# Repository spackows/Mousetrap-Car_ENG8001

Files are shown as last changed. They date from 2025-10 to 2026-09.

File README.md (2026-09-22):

# Mousetrap Car
Group project for: **ENG8001 - Principles of Design**, [Bachelor of Engineering (Automation and Robotics Engineering) (Co-op)](https://www.algonquincollege.com/sat/program/bachelor-of-automation-and-robotics/)

<p>&nbsp;</p>

## Background

### Mousetrap cars in STEM education
Sooner or later, most science, engineering, or design students build a [mousetrap car](https://en.wikipedia.org/wiki/Mousetrap_car). :)

Details vary, but most projects focus on building a small car that is powered by a spring-loaded bar type of mousetrap. Mousetrap car builders sometimes compete to see who can build a car that achieves maximum speed or maximum distance.

### Our project goals
1. Build a mousetrap car that travels 20 feet as efficiently as possible while autonomously navigating around an 8-inch x 4-inch obstacle at a variable distance in the center of a 4-foot-wide track.
2. Learn to apply engineering design principles and practices.

<p>&nbsp;</p>

## Design conception

### Objectives
We identified 5 objectives:
1. Go fast – Be in the top 25% fastest results
2. Sense object – Detect object 100% of the time
3. Avoid object – Avoid the object 100% of the time
4. Stay on the track/cross the finish – Even if we are not the fastest, complete the course every run
5. Consistent performance – Successfully detect and avoid the object every run; and the time of our runs will not vary by more than 10%

To prioritize these objectives, we used a pairwise comparison matrix.  For each cell, a 1 is assigned if the objective in that row is more important than the objective in that column.  Then, for each row, the sum of the 1's is the score for the objective in that row.

Table 1: Pairwise comparison of objectives
<table>
<tr>
<td>&nbsp;</td>
<td align="center">Go fast</td>
<td align="center">Sense object</td>
<td align="center">Avoid object</td>
<td align="center">Stay on track</td>
<td align="center">Consistent</td>
<td align="center"><b>Score</b></td>
</tr>
<tr>
<td>Go fast</td>
<td align="center">x</td>
<td align="center">0</td>
<td align="center">0</td>
<td align="center">0</td>
<td align="center">1</td>
<td align="center"><b>1</b></td>
</tr>
<tr>
<td>Sense object</td>
<td align="center">1</td>
<td align="center">x</td>
<td align="center">0</td>
<td align="center">0</td>
<td align="center">1</td>
<td align="center"><b>2</b></td>
</tr>
<tr>
<td>Avoid object</td>
<td align="center">1</td>
<td align="center">1</td>
<td align="center">x</td>
<td align="center">1</td>
<td align="center">1</td>
<td align="center"><b>4</b></td>
</tr>
<tr>
<td>Stay on track</td>
<td align="center">1</td>
<td align="center">1</td>
<td align="center">0</td>
<td align="center">x</td>
<td align="center">1</td>
<td align="center"><b>3</b></td>
</tr>
<tr>
<td>Consistent</td>
<td align="center">0</td>
<td align="center">0</td>
<td align="center">0</td>
<td align="center">0</td>
<td align="center">x</td>
<td align="center"><b>0</b></td>
</tr>
</table>

### Key functions
We identified key functions:
1. How is power transferred from the spring to the wheels?
2. How is the object sensed?
3. How is the object avoided?
4. How is steering accomplished?
5. How will the car stay on the track?
6. How will speed be optimized?

We used a morphological table to define the space of our early conceptual solutions.

Table 2: Morphological table
<table>
<tr>
<td align="center"><b>Function</b></td>
<td  align="center" colspan="3"><b>Means</b></td>
</tr>
<tr>
<td valign="top">Transfer power from spring</td>
<td valign="top">Tie a string from the hammer to around the axle</td>
<td valign="top">Attach an extension to the hammer and tie the string to that for greater leverage</td>
<td valign="top">Attach a "foot" to the hammer so that when the spring unwinds, the foot pushes against the ground</td>
</tr>
<tr>
<td valign="top">Sense object</td>
<td valign="top">Ultrasonic sensor</td>
<td valign="top">Camera</td>
<td valign="top">"Feeler" (like antennae or whiskers)</td>
</tr>
<tr>
<td valign="top">Avoid object</td>
<td valign="top">Steer around the object</td>
<td valign="top">Jump over the object</td>
<td valign="top">Use the object itself to push the car around (like a spinning bumper)</td>
</tr>
<tr>
<td valign="top">Stay on Track</td>
<td valign="top">Detect the tape at the edges using a camera and steer away from them</td>
<td valign="top">Steer a trajectory that passes close to the object (because it’s in the middle)</td>
<td valign="top">Programmatically limit steering to maintain an overall straight displacement</td>
</tr>
<tr>
<td valign="top">Steering</td>
<td valign="top">Use a motor to pivot the front axle</td>
<td valign="top">Use a weight to lean to turn the wheels (like a skateboard)</td>
<td valign="top">Temporarily drop an anchor to pull the car to the left or right</td>
</tr>
<tr>
<td valign="top">Speed</td>
<td valign="top">Use 3 wheels instead of 4 to reduce friction from wheels</td>
<td valign="top">Make the car aerodynamic</td>
<td valign="top">Start the car on an angle to reduce the number of turns needed</td>
</tr>
</table>

### Sketches
Whiteboard sketches from brainstorming concepts:

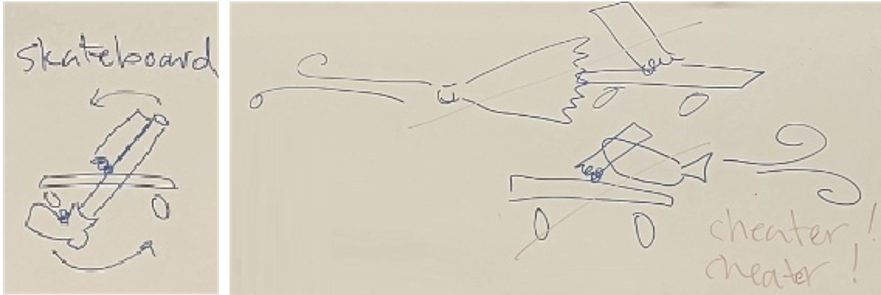
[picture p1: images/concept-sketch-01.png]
<br/>
Figure 1: Sketches of ways to transfer energy from the spring into motion. Left: Attachment to spring pushes on the ground (like a person on a skateboard.)  Right: Squashing air from a bellows or whoopee cushion – deemed not allowed.

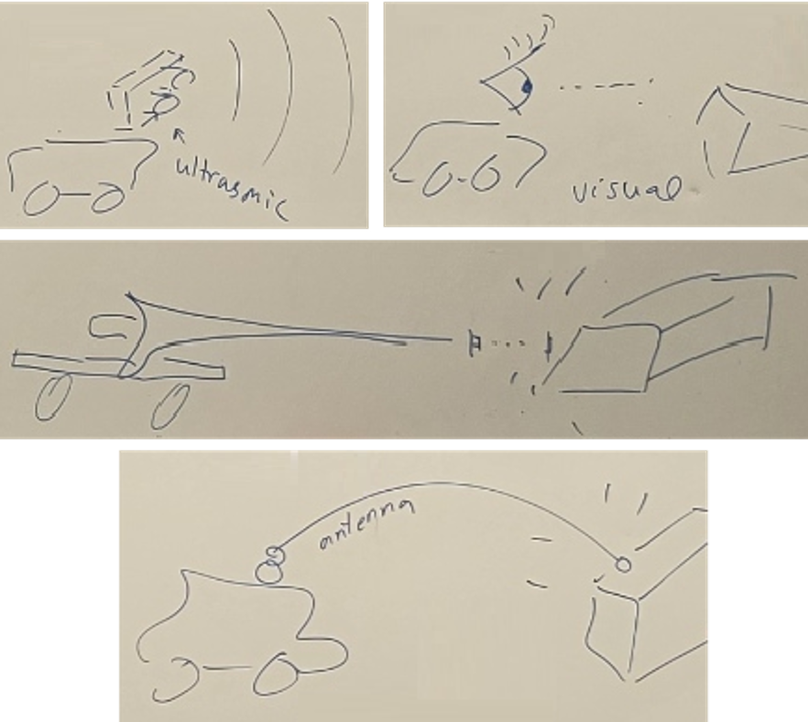
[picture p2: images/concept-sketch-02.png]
<br/>
Figure 2: Sketches of ways to sense the object.  Top left: ultrasonic sensor.  Top right: camera.  Middle: Touching the object with a rigid, forward extension (like a lance.)  Bottom: Feelers (like whiskers or antennae.)

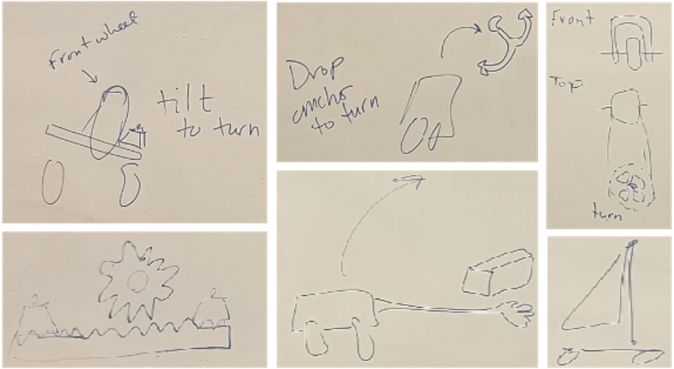
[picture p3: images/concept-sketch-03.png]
<br/>
Figure 3: Sketches of ways to steer.  Top left: tilt the vehicle (like a bicycle or skateboard.) Bottom left: method of tilting. Top middle: touch the ground and pivot.  Bottom middle: pivot around the wood block.  Top right: turn the wheel with a motor.  Bottom right: use a sail like a rudder to turn.

<p>&nbsp;</p>

## Testing
We developed a set of parameters for our selected concepts and a reasonable set of levels for each parameter:
- **Drive wheel diameter** – How large is just right for our situation? Levels (3): 50mm, 75mm, 100mm
- **Axle grip** – How to decrease the slipping of the string on the driving axle? Levels (3): bare wood, axle with grippy substance, hook on the axle
- **Hammer arm vs. wheel** – Is there a benefit to allowing the spring to turn more than 180°? Levels (2): Regular mousetrap with an arm attached to the hammer, spring with no wood and a wheel attached to the hammer
- **Hammer arm/wheel size** – How large is just right for our situation. Levels (3): 50mm, 100mm, 150mm
- **Powertrain layout** – Is front-wheel drive or rear-wheel drive faster? Levels (2): front-wheel drive, rear-wheel drive
- **Object detection method** – How to detect the obstacle? Levels (3): whisker sensor, ultrasonic sensor, camera
- **Steering method** – How to steer? Levels (2): motor turn directly, lean to turn

Table 3: Parameters and levels
<table>
<tr>
<td colspan="2">&nbsp;</td>
<td><b>1</b></td>
<td><b>2</b></td>
<td><b>3</b></td>
</tr>
<tr>
<td><b>A</b></td>
<td>Drive wheel diameter (mm)</td>
<td>50</td>
<td>75</td>
<td>100</td>
</tr>
<tr>
<td><b>B</b></td>
<td>Axle grip</td>
<td>Bare wood</td>
<td>Axle with grippy substance applied</td>
<td>Hook on the axle</td>
</tr>
<tr>
<td><b>C</b></td>
<td>Hammer arm vs. wheel</td>
<td>Arm</td>
<td>Wheel</td>
<td>x</td>
</tr>
<tr>
<td><b>D</b></td>
<td>Hammer arm/wheel size (mm)</td>
<td>50</td>
<td>100</td>
<td>150</td>
</tr>
<tr>
<td><b>E</b></td>
<td>Powertrain layout</td>
<td>Front</td>
<td>Rear</td>
<td>x</td>
</tr>
<tr>
<td><b>F</b></td>
<td>Object detection</td>
<td>Whisker</td>
<td>Ultrasonic</td>
<td>Camera</td>
</tr>
<tr>
<td><b>G</b></td>
<td>Steering</td>
<td>Motor turn</td>
<td>Lean</td>
<td>x</td>
</tr>
</table>

To perform full factorial testing with 7 factors and up to 3 levels would require on the order of (levels)(factors) : 37 = 2187 tests. That’s a lot of tests to run! So, we used a [Taguchi orthogonal matrix](https://www.york.ac.uk/depts/maths/tables/orthogonal.htm) to reduce the number of tests to run.

Unfortunately, there is no 7-factor, mixed-level Taguchi orthogonal matrix available to copy. So, we wrote a [Python script](https://github.com/spackows/Mousetrap-Car_ENG8001/blob/main/code-snippets/Adjust-Taguchi-matrix_2025-11-06.py) to convert a 13-factor, 3-level Taguchi orthogonal matrix (27 rows) for our purposes.

<p>&nbsp;</p>

## Final design 

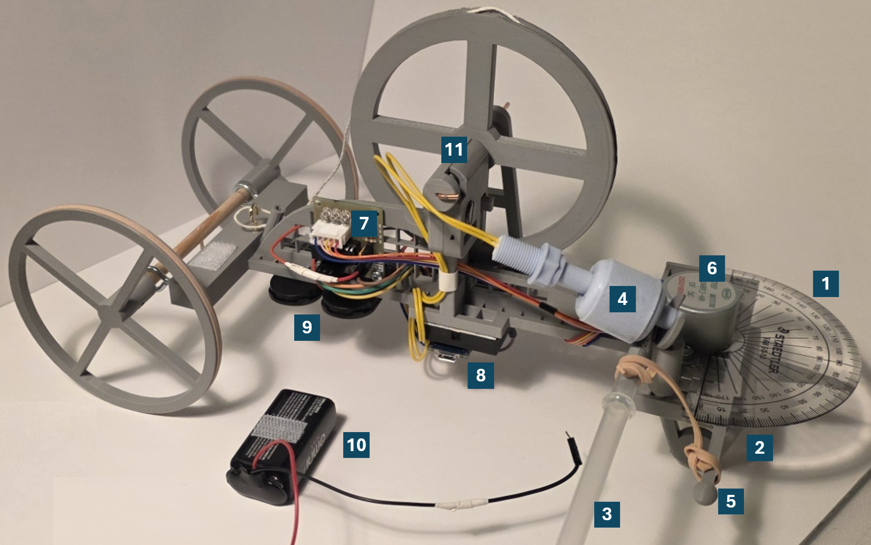
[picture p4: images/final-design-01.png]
<br/>
Figure 4: Side view

1. Our strategy was to aim our car just to the left of the object from the start line so that the car only had to make one right turn after passing the object.  We attached a protractor to ensure our front wheel was perfectly aimed.
2. Our car had one front wheel; and the whole axle pivoted to turn.  *See Figure 5 for details.*
3. A plastic straw acted as our whisker to detect the obstacle.  *See Figure 6 for multiple views.*
4. When the car passed close by the obstacle, the whisker was pushed backwards on the car by the obstacle, raising the float sensor, signalling to turn right after a short delay.  (Calculating how much to turn the wheel was based on a real-time measurement of how long the car had been traveling since being released at the start line.)
5. The whisker was attached to a post with an elastic to prevent the whisker from falling back due to the car's acceleration at the start.
6. The front axle was turned by a [28BYJ-48 stepper motor](https://www.makerguides.com/wp-content/uploads/2019/04/28byj48-Stepper-Motor-Datasheet.pdf).
7. The driver board for the stepper motor was screwed to the chassis in a way that made accessing the pins easy.
8. An [Arduino Nano 33 IoT](https://docs.arduino.cc/hardware/nano-33-iot/) was attached to the bottom of the chassis in a way that made attaching a micro-USB cable easy.
9. One pair of 3V button cell batteries powered the stepper motor and one pair powered the Arduino.
10. The button cell batteries were chosen for their light weight.  But they lost power after only a few runs.  So, during testing, we temporarily attached a 9V battery.
11. We removed the spring from the mousetrap and used it to turn a wheel that pulled a string wrapped around the rear axle. *See Figure 7 for details.*

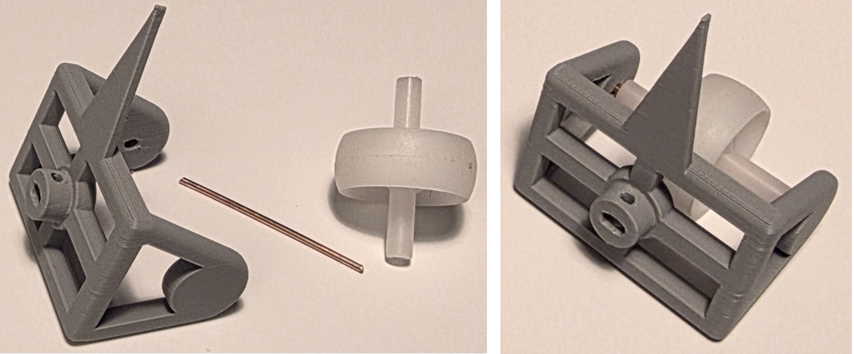
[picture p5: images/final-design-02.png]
<br/>
Figure 5: Front axle and wheel

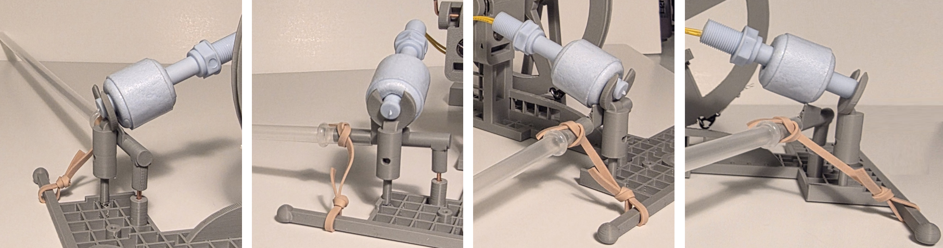
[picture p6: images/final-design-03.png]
<br/>
Figure 6: Views of the whisker

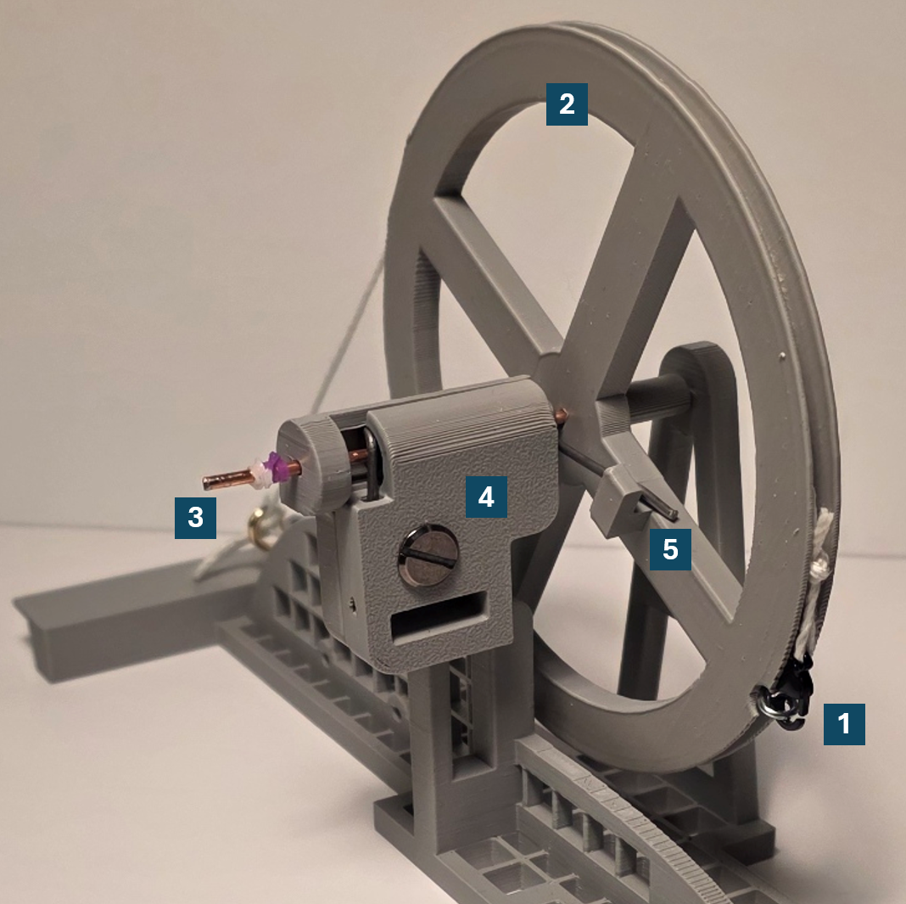
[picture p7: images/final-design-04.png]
<br/>
Figure 7: Spring tower

We reasoned that because the mousetrap snaps shut with great force, there must be unused energy in the spring when only turned through 180°. Removing the spring from the wooden board of the trap and encasing it in the spring tower made it possible to get more energy from the spring - through nearly 360°.

1. String wrapped around the rear axle was draped around the circumference of a large drive wheel.
2. The drive wheel was powered by the mousetrap spring.
3. The drive wheel and mousetrap spring were mounted in a central axle.
4. The spring was held securely in place by a specially designed housing that made it easy to replace the spring after one or two uses (when the spring lost its springiness).
5. One arm of the spring hooked onto the drive wheel, and the drive wheel was manually rotated to load the spring before releasing the car at the start of the track.

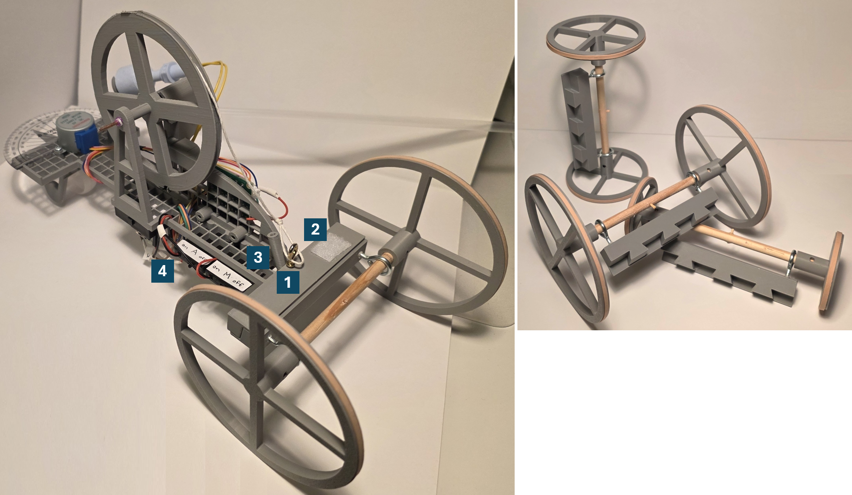
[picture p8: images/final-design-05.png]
<br/>
Figure 8: Read view

1. The rear axle and wheels were detachable to make it easier to transport the car to and from class and to make it easier to test different wheel sizes.
2. The 9V battery was temporarily attached to the car by velcro during testing.
3. Because aiming the car just to the left of the obstacle was a critical part of our strategy, a long bamboo stick (a shish kabob stick) could be secured in a holder. This enabled us to visually align the nose of the car with the stick for better aim.
4. The button cell battery holders had on-off switches so we could save the power in the batteries.  The holders were labelled with stickers to make it easy to know which batteries powered which part of the solution.

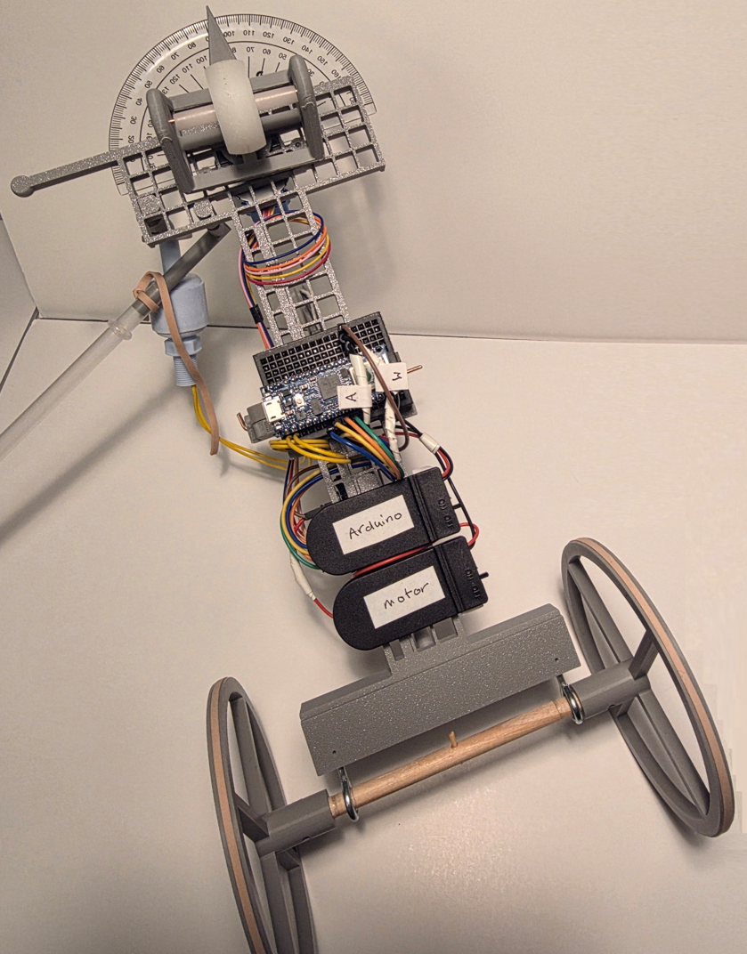
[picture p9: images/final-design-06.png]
<br/>
Figure 9: With the shish kabob stick removed, the chassis could sit upside down for easy access to wiring, batteries, and the Arduino.  The battery holder and wires were labelled on the bottom too.

<p>&nbsp;</p>

## Discussion
Our team designed a solution that met the given basic requirements.  Our car made the distance and successfully detected and avoided the obstacle.  

However, we also leaned into exploring quirky solutions, such as aiming the car just to the left of the obstacle, sensing the obstacle by touch, and getting more energy from the spring by removing it from the mousetrap board.  

In addition, we spent considerable effort designing a solution that was modular, to make it easy to transport and to switch components during iterative development.  

Finally, a significant focus of our design was ease of maintenance: designing the chassis to sit upside down; carefully positioning the batteries, stepper motor driver board, and Arduino for easy access; and labeling components and wires.

Children can have fun building mousetrap cars.  Of course, requiring that the car autonomously sense and avoid an obstacle increased the technical challenge.  But a mousetrap car project can also be used to learn how to apply rigorous engineering design practices, such as: objectives prioritization through pairwise comparison; systematic exploration of conceptual solutions through the use or morphological tables; test plan creation, including the use of Taguchi orthogonal matrices to reduce the number of tests while still covering required functionality; and writing formal reports at different stages of design and development.

<p>&nbsp;</p>

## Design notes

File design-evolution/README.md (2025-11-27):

## Features
<ul>
<li><a href="">Rear wheels</a></li>
<li><a href="">Transferring power from spring to wheels</a></li>
<li><a href="">Chassis</a></li>
<li><a href="">Detecting the object</a></li>
<li><a href="">Steering the car</a></li>
</ul>

<p>&nbsp;</p>

## Rear wheels

<table>
<tr><th>Iteration</th><th>Discussion</th><th>Images</th></tr>
<tr>
<td valign="top"><p>1</p></td>
<td valign="top">
<p>Cardboard</p>
<ul>
<li>Cardboard circle (from cake decorating store)</li>
<li>Attached to axle with open end of Chicago screw</li>
<li>Chicago screw pokes through cardboard and taped on</li>
</ul>
</td>
<td valign="top">

</td>
</tr>
<tr>
<td valign="top"><p>2</p></td>
<td valign="top">
<p>3D printed</p>
<ul>
<li>3D printed wheels of various diameters</li>
<li>Cut-outs to reduce weight</li>
<li>Groove on outer edge to hold elastic band for traction</li>
<li>Flange type attachement to the axle</li>
</ul>
</td>
<td valign="top">
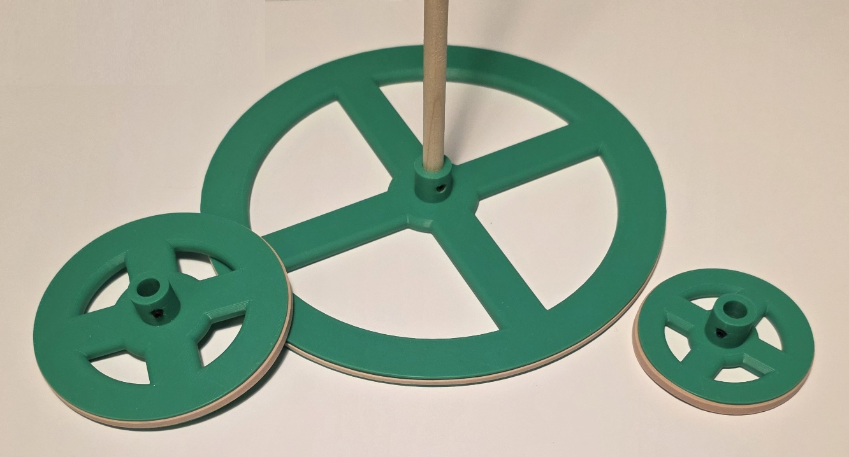
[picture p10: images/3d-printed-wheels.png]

</td>
</tr>
</table>

<p>&nbsp;</p>

## Transferring power from spring to wheels

<table>
<tr><th>Iteration</th><th>Discussion</th><th>Images</th></tr>
<tr>
<td valign="top"><p>1</p></td>
<td valign="top">
<p>Straight arm medium</p>
<ul>
<li>Arm length 130cm (spring centre to string attachment)</li>
<li>Arm lashed to mousetrap hammer with wire</li>
<li>Fishing line attaches arm to axel</li>
<li>Fishing line tied to top of arm</li>
<li>Fishing line wrapped around plain wooded axel</li>
</ul>
</td>
<td valign="top">
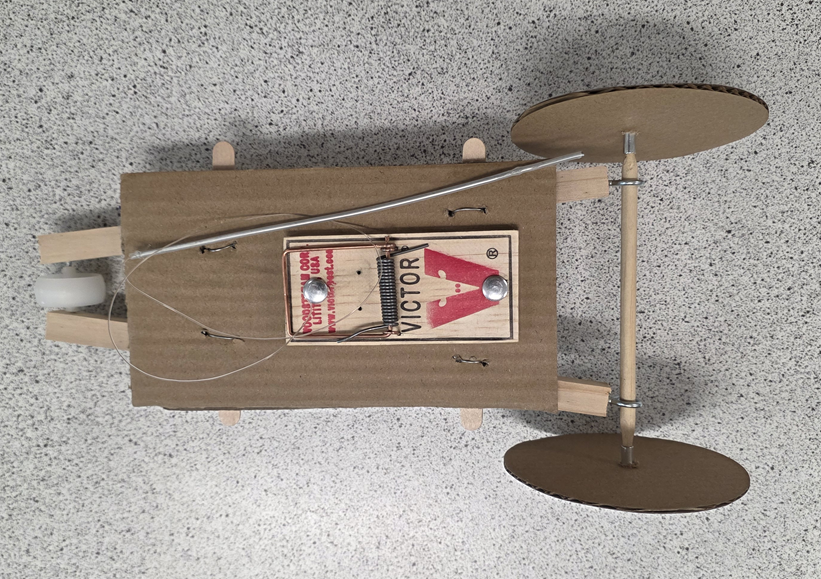
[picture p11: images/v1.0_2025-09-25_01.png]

</td>
</tr>
<tr>
<td valign="top"><p>2</p></td>
<td valign="top">
<p>Hammer 360</p>
<ul>
<li>Mousetrap spring removed from the wood</li>
<li>Support structure to allow the spring to rotate as far as possible (~360°)</li>
<li>Arm lashed to the hammer</li>
</ul>
</td>
<td valign="top">
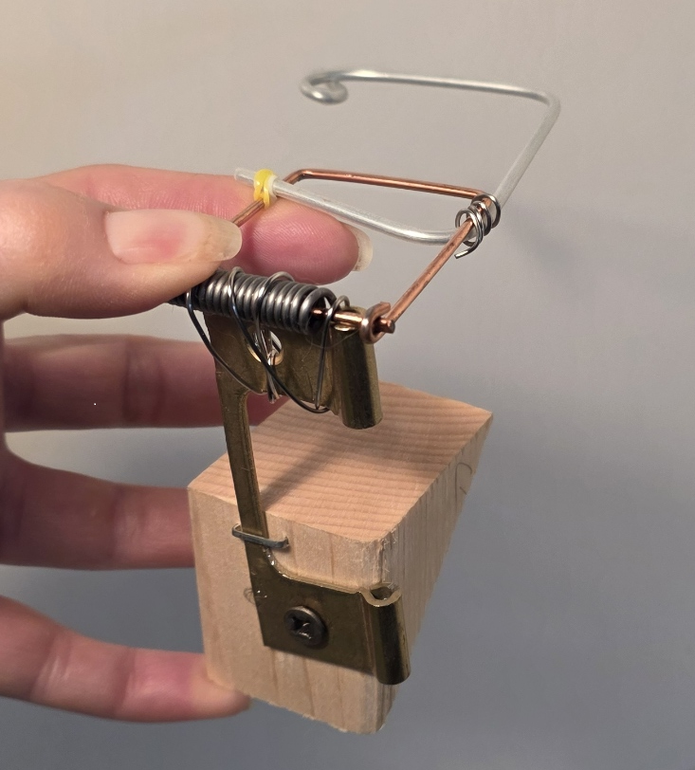
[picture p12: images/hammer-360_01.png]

</td>
</tr>
<tr>
<td valign="top"><p>3</p></td>
<td valign="top">
<p>Spring tower</p>
<ul>
<li>Mousetrap spring removed from the wood</li>
<li>3D-printed support structure to allow the spring to rotate as far as possible (~360°)</li>
</ul>
</td>
<td valign="top">
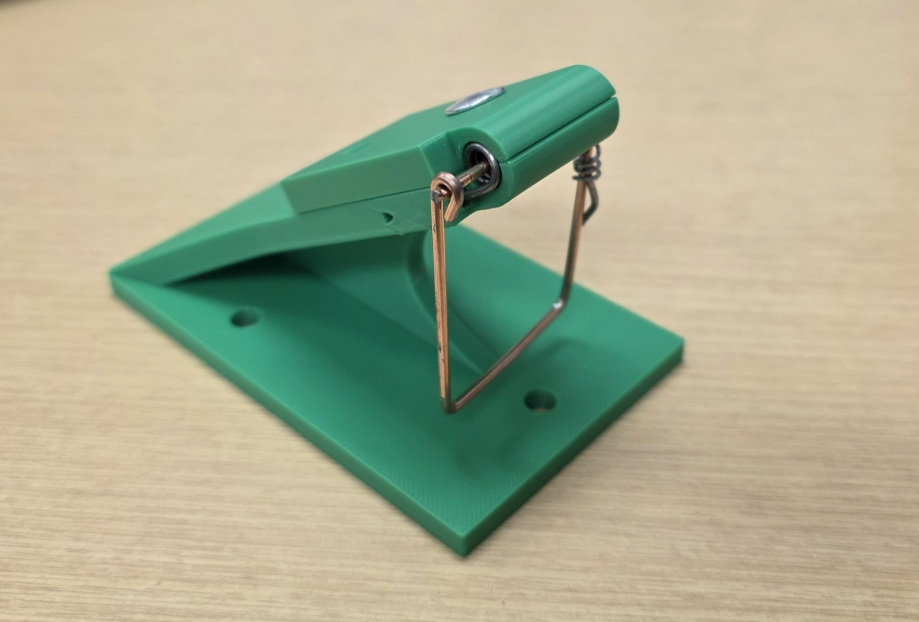
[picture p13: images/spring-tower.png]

</td>
</tr>
<tr>
<td valign="top"><p>4</p></td>
<td valign="top">
<p>Spring wheel</p>
<ul>
<li>Mousetrap wood and hammer removed from the spring</li>
<li>Support structure to allow the spring to rotate as far as possible (~360°)</li>
<li>Wheel is turned by the spring</li>
<li>Groove on wheel outside keeps string in place</li>
</ul>
</td>
<td valign="top">
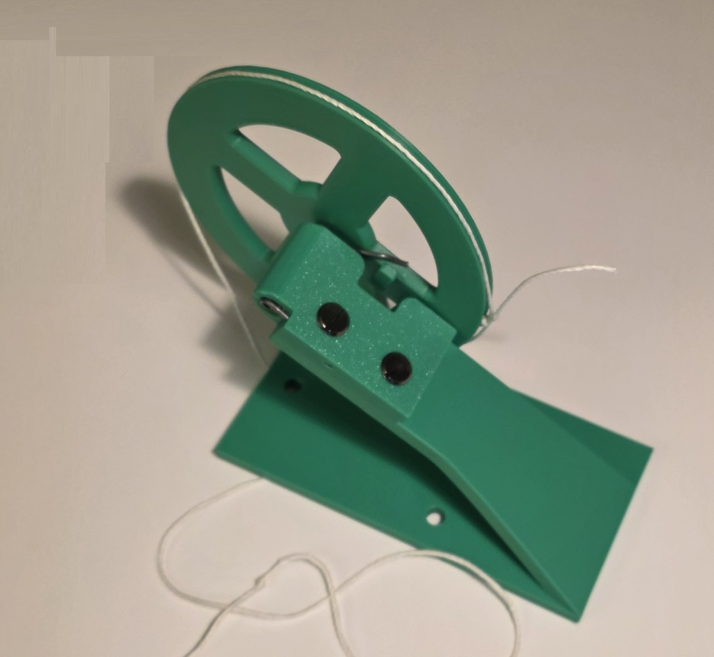
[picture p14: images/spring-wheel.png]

</td>
</tr>
<tr>
<td valign="top"><p>4</p></td>
<td valign="top">
<p>Full drivetrain</p>
<ul>
<li>Spring support structure and wheel mounted on chassis</li>
<li>String winds around the drive axle</li>
<li>Axle has little stick to keep the string from slipping at the end of unwinding</li>
</ul>
</td>
<td valign="top">
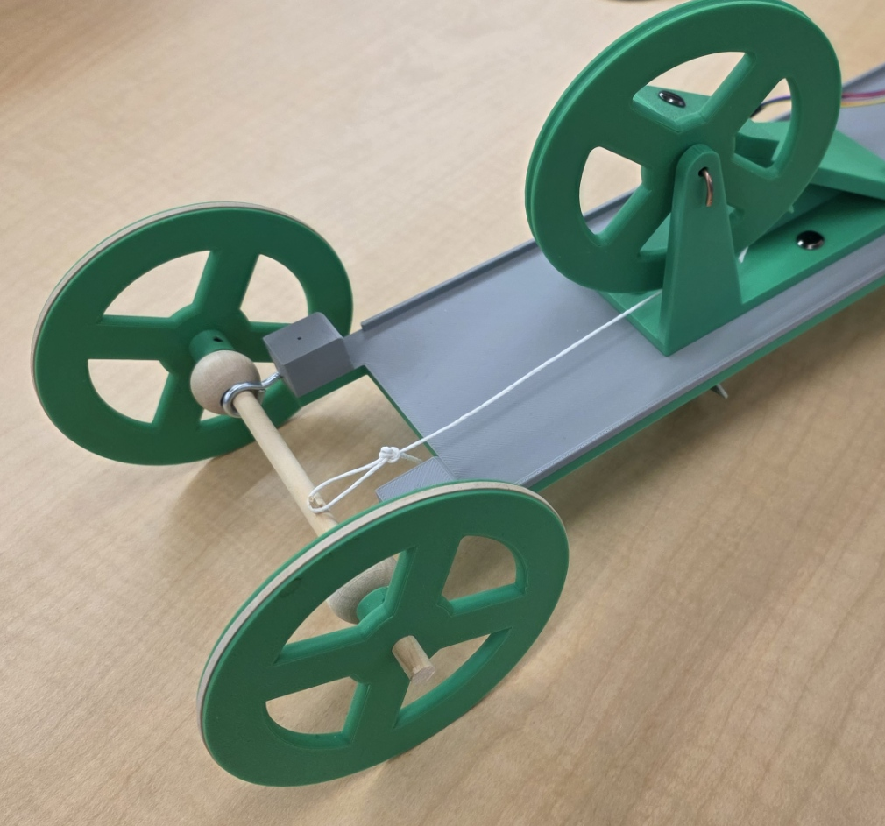
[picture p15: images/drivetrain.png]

</td>
</tr>
</table>

<p>&nbsp;</p>

## Chassis

<table>
<tr><th>Iteration</th><th>Discussion</th><th>Images</th></tr>
<tr>
<td valign="top"><p>1</p></td>
<td valign="top">
<p>Initial</p>
<ul>
<li>Frame of wood sticks</li>
<li>Cardboard bed</li>
<li>Chicago screws hold mousetrap</li>
<li>Eyelets hold axle</li>
</ul>
</td>
<td valign="top">
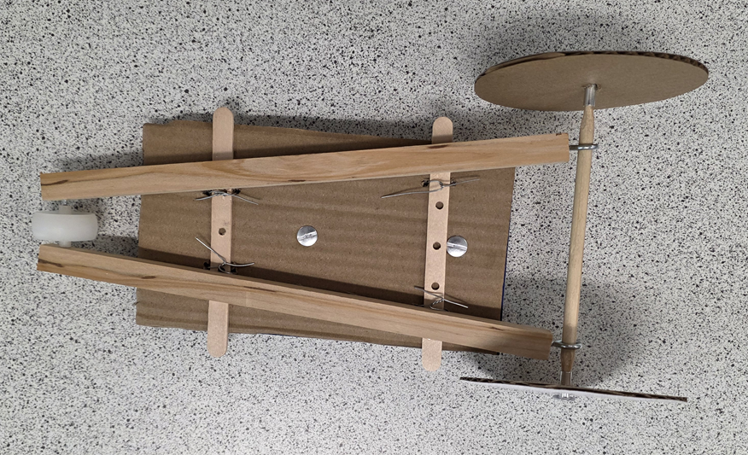
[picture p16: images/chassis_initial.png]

</td>
</tr>
<tr>
<td valign="top"><p>2</p></td>
<td valign="top">
<p>First 3D print</p>
<ul>
<li>Wide enough for Arduino breadboards</li>
<li>Holes for stepper motor at front</li>
<li>Holes for either mousetrap or spring tower</li>
</ul>
</td>
<td valign="top">
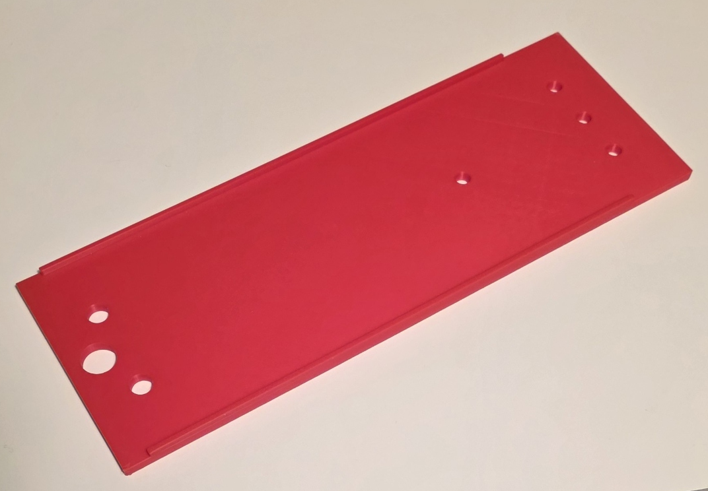
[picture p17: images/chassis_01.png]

</td>
</tr>
<tr>
<td valign="top"><p>3</p></td>
<td valign="top">
<p>v2</p>
<ul>
<li>New axle design</li>
</ul>
</td>
<td valign="top">
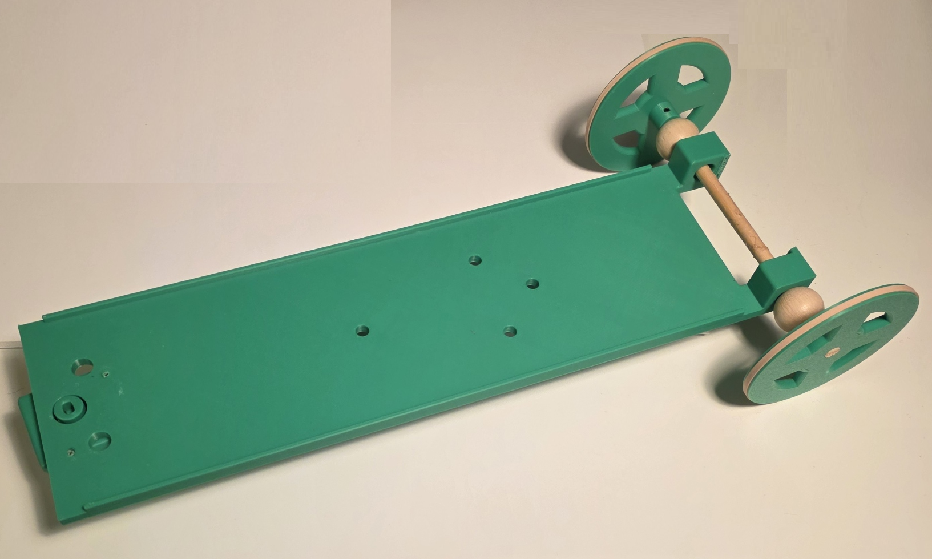
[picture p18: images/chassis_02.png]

</td>
</tr>
<tr>
<td valign="top"><p>4</p></td>
<td valign="top">
<p>v3</p>
<ul>
<li>Can have eyelets on top for large wheels</li>
<li>Can have eyelets on back for medium wheels</li>
<li>Can have eyelets on bottom for small wheels</li>
</ul>
</td>
<td valign="top">
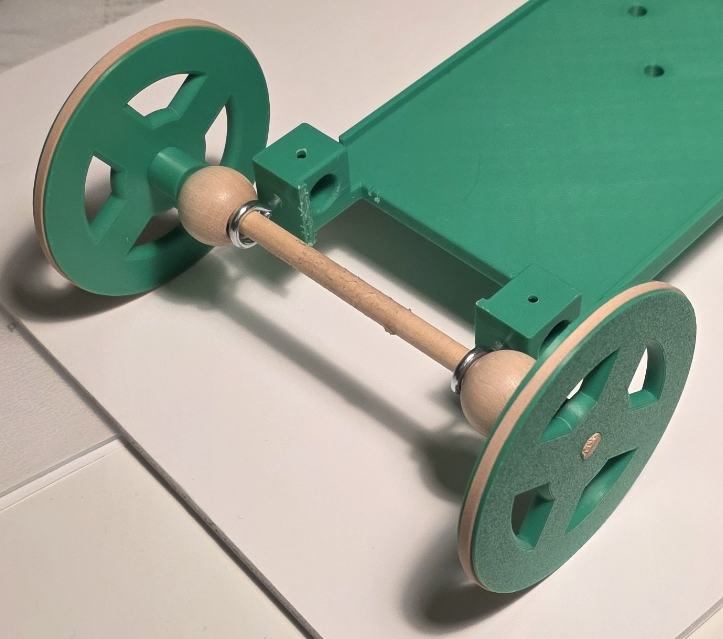
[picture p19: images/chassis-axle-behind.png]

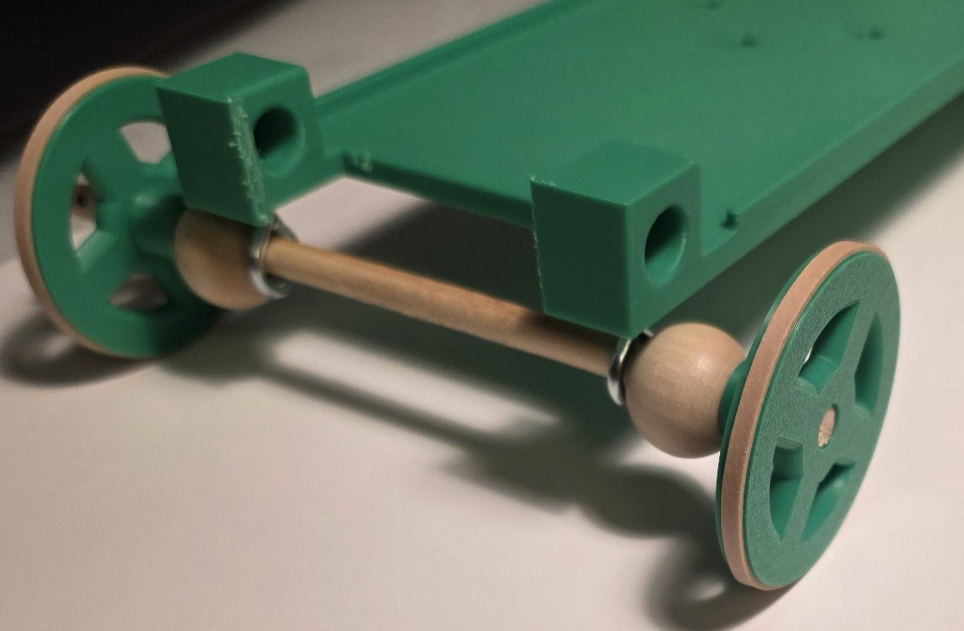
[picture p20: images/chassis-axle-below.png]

</td>
</tr>
<tr>
<td valign="top"><p>5</p></td>
<td valign="top">
<p>With protractor</p>
<ul>
<li>Holds protractor at front</li>
<li>Can hold a mousetrap, or it can hold a spring tower facing forward or backward</li>
</ul>
</td>
<td valign="top">
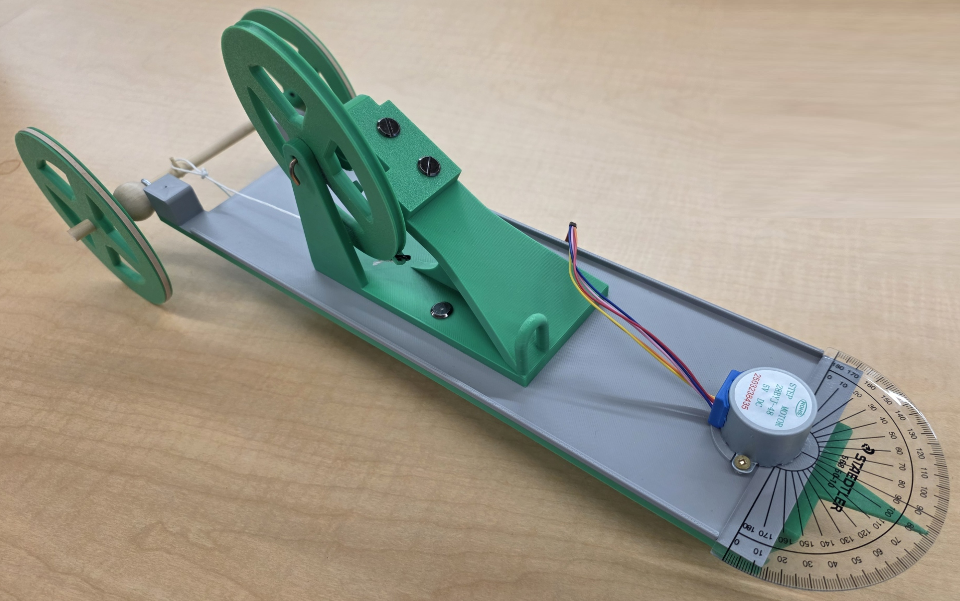
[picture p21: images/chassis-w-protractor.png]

</td>
</tr>
<tr>
<td valign="top"><p>6</p></td>
<td valign="top">
<p>With sight wire</p>
<ul>
<li>Vertical wire at back of chassis can be aligned with the pointer on the front wheel to precisely  aim where the car is going</li>
</ul>
</td>
<td valign="top">

</td>
</tr>
</table>

<p>&nbsp;</p>

## Detecting the object

<p>&nbsp;</p>

## Steering the car

<table>
<tr><th>Iteration</th><th>Discussion</th><th>Images</th></tr>
<tr>
<td valign="top"><p>1</p></td>
<td valign="top">
<p>No turn</p>
<ul>
<li>Single wheel</li>
<li>Axle fixed to chassis</li>
</ul>
</td>
<td valign="top">
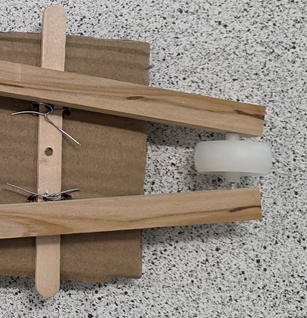
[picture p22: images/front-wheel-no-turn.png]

</td>
</tr>
<tr>
<td valign="top"><p>2</p></td>
<td valign="top">
<p>Swivel</p>
<ul>
<li>Single wheel</li>
<li>Axle fixed to swivel</li>
<li>Hole at top of swivel to attach to a motor</li>
</ul>
</td>
<td valign="top">
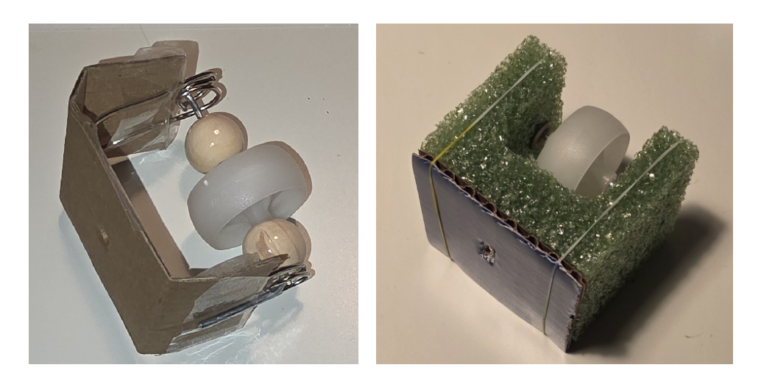
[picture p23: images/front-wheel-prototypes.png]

</td>
</tr>
<tr>
<td valign="top"><p>3</p></td>
<td valign="top">
<p>Flange-inspired</p>
<ul>
<li>Single wheel</li>
<li>Axle fixed to swivel</li>
<li>Flange type attachement at top to attach to a motor</li>
</ul>
</td>
<td valign="top">
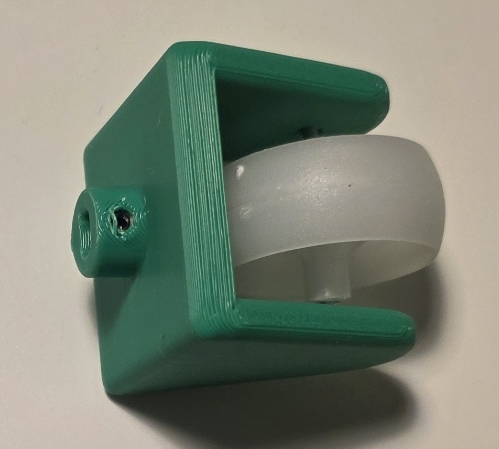
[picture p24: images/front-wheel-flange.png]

</td>
</tr>
<tr>
<td valign="top"><p>4</p></td>
<td valign="top">
<p>Wheel pointer</p>
<ul>
<li>Pointer is added to the swivel to show the direction the wheel is facing</li>
<li>Swivel is wider to allow more wheel extension to cover a longer axle (for less wiggle)</li>
</ul>
</td>
<td valign="top">
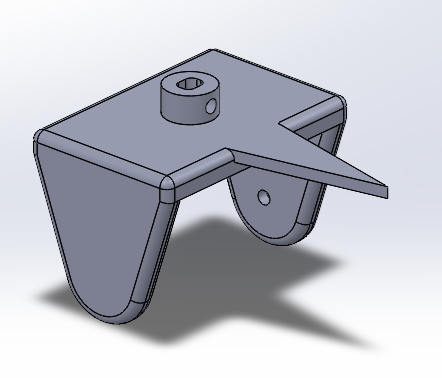
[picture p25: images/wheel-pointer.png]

</td>
</tr>
<tr>
<td valign="top"><p>5</p></td>
<td valign="top">
<p>Protractor</p>
<ul>
<li>Wheel is attached to stepper moter on chassis</li>
<li>Protractor is attached to chassis, centered on stepper motor arm</li>
<li>Angle of wheel turn can be read by the angle to which the wheel pointer aligns on the protractor</li>
</ul>
</td>
<td valign="top">
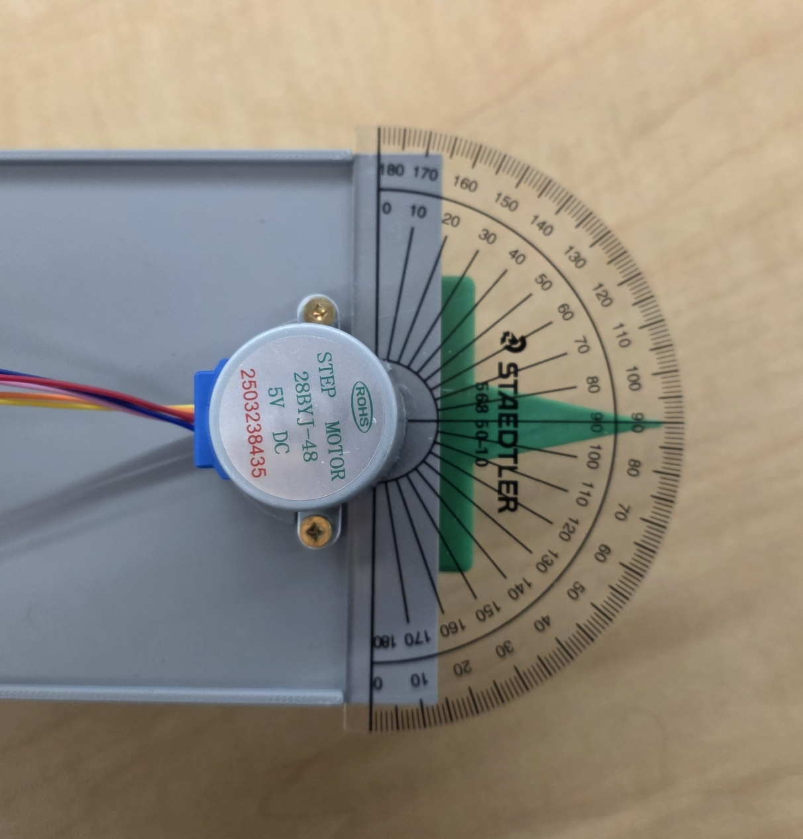
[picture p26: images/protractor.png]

</td>
</tr>
</table>

<p>&nbsp;</p>

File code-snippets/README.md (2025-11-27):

<table>
<tr><th>File</th><th>Description</th></tr>
<tr>
<td valign="top">
<a href="">Button.ino</a>
</td>
<td valign="top">
Prints status of the button to the serial monitor.  0 is pressed, 1 is unpressed.
</td>
</tr>
<tr>
<td valign="top">
<p><a href="flow-meter_01.ino">flow-meter_01.ino</a></p>
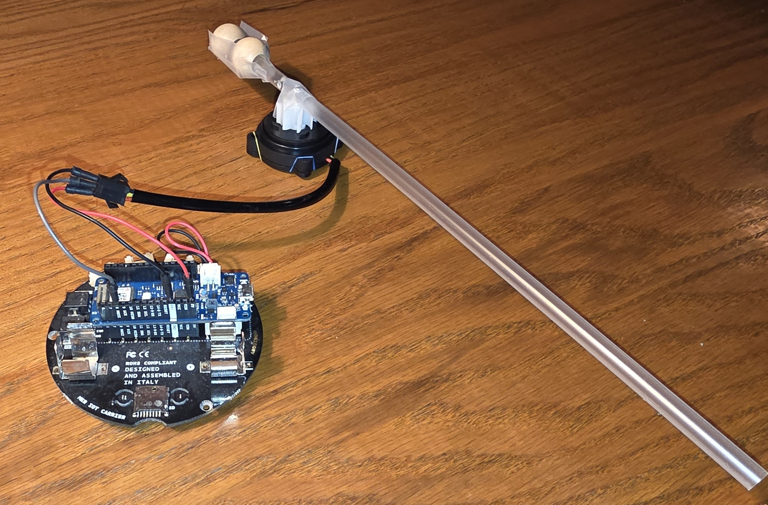
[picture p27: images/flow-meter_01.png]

</td>
<td valign="top">
<p>Prints status of the flow pin to the console, lights up after the sensor has been activated</p>
<ul>
<li>Board: <a href="https://docs.arduino.cc/hardware/mkr-wifi-1010/#tech-specs">MKR WiFi 1010</a></li>
<li>Sensor: <a href="https://www.digiten.shop/products/digiten-g3-4-water-flow-hall-sensor-switch-flow-meter-1-60l-min">DIGITEN G3/4" Water Flow Hall Sensor Switch Flow Meter 1-60L/min</a></li>
<li>Inspiration: <a href="https://medium.com/@sarah-packowski/did-you-leave-the-hose-running-638365910afd">Blog post</a></li>
</ul>
</td>
</tr>
<tr>
<td valign="top">
<p><a href="float-meter_01.ino">float-meter_01.ino</a></p>
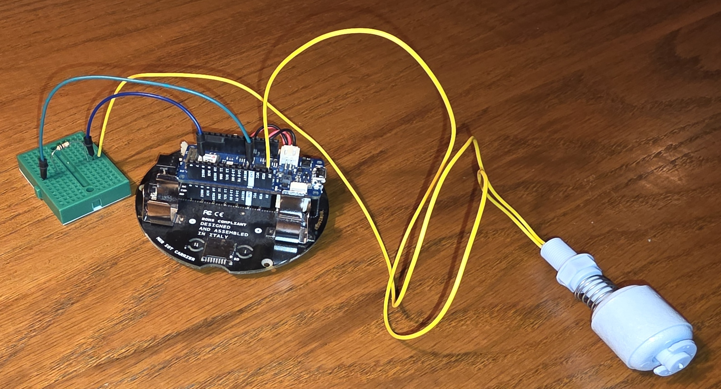
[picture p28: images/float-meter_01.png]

</td>
<td valign="top">
<p>Prints status of the float sensor to the console, lights up after the sensor has been activated</p>
<ul>
<li>Board: <a href="https://docs.arduino.cc/hardware/mkr-wifi-1010/#tech-specs">MKR WiFi 1010</a></li>
<li>Sensor: <a href="https://www.amazon.ca/dp/B07RXVPQL4?ref_=ppx_hzsearch_conn_dt_b_fed_asin_title_2">Keenso Water Level Sensor Vertical Float Switch</a></li>
<li>Inspiration: <a href="https://medium.com/@sarah-packowski/keep-water-from-overflowing-with-a-float-sensor-2c753d94a4ae">Blog post</a></li>
</ul>
</td>
</tr>
<tr>
<td valign="top">
<p><a href="stepper-motor_01.ino">stepper-motor_01.ino</a></p>

</td>
<td valign="top">
<p>Simply spins the motor</p>
<ul>
<li>Board: <a href="https://docs.arduino.cc/hardware/mkr-wifi-1010/#tech-specs">MKR WiFi 1010</a></li>
<li>Motor: <a href="https://www.makerguides.com/wp-content/uploads/2019/04/28byj48-Stepper-Motor-Datasheet.pdf">28BYJ-48 stepper motor</a></li>
<li>Driver board: <a href="https://www.hadex.cz/spec/m513.pdf">ULN2003 driver board</a></li>
<li>Power supply module: <a href="https://components101.com/modules/5v-mb102-breadboard-power-supply-module">MB102 Breadboard power supply module</a></li>
<li>Inspiration: <a href="https://github.com/NikodemBartnik/ArduinoTutorials/blob/master/28BYJ-48/28BYJ-48.ino">Sample by Nikodem Bartnik</a></li>
</ul>
</td>
</tr>
<tr>
<td valign="top">
<p><a href="stepper-motor_02.ino">stepper-motor_02.ino</a></p>
</td>
<td valign="top">
<p>Everything is the same as <a href="stepper-motor_01.ino">stepper-motor_01.ino</a>, except...</p>
<p>This one turns the motor by a specified angle (in degrees)</p>
</td>
</tr>
</table>

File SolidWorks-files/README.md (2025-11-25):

<table>
<tr>
<th>Thumbnail</th>
<th>File and description</th>
</tr>
<!---------------------------------- Small drive wheel -->
<tr>
<td valign="top">
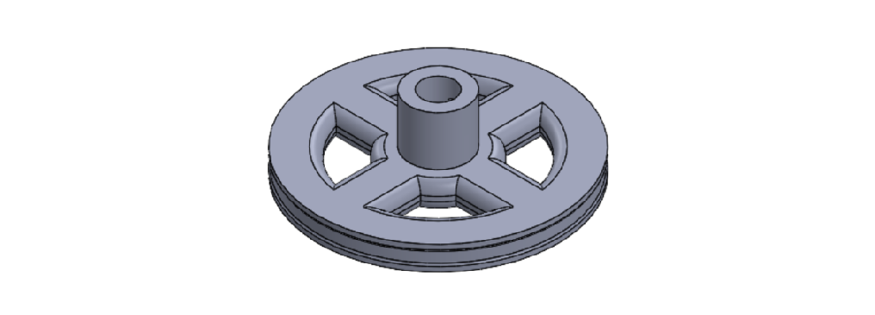
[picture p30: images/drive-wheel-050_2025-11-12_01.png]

</td>
<td valign="top">
<p><a href="drive-wheel-050_2025-11-12_01.SLDPRT">drive-wheel-050_2025-11-12_01</a></p>
<p>Small drive wheel (wheel attached to axle being driven by spring)</p>
</td>
</tr>
<!---------------------------------- Medium drive wheel -->
<tr>
<td valign="top">
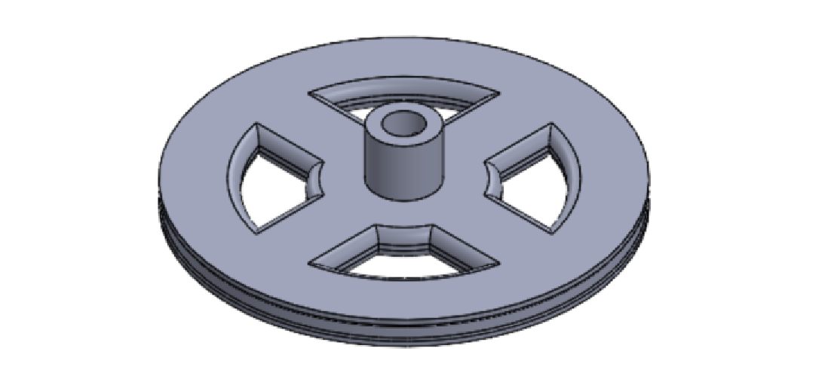
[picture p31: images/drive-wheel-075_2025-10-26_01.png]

</td>
<td valign="top">
<p><a href="drive-wheel-075_2025-10-26_01.SLDPRT">drive-wheel-075_2025-10-26_01</a></p>
<p>Medium drive wheel (wheel attached to axle being driven by spring)</p>
</td>
</tr>
<!---------------------------------- Large drive wheel -->
<tr>
<td valign="top">
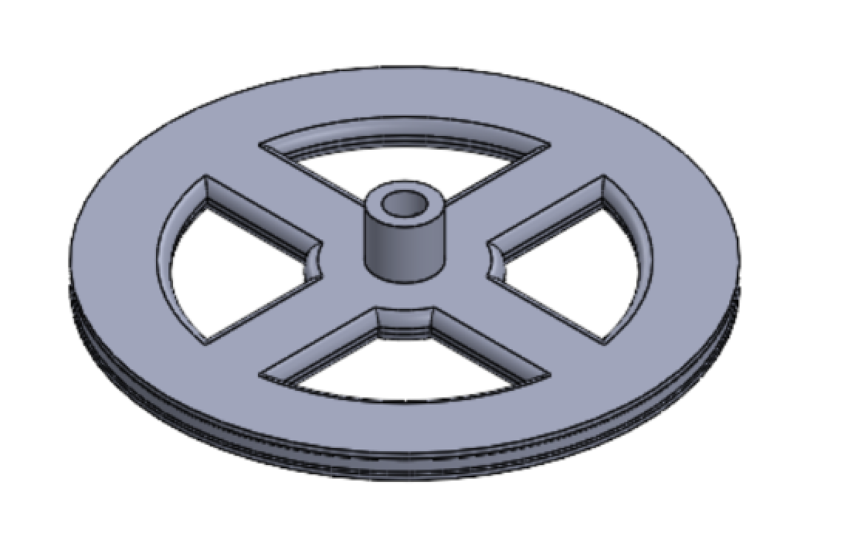
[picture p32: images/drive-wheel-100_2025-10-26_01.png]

</td>
<td valign="top">
<p><a href="drive-wheel-100_2025-10-26_01.SLDPRT">drive-wheel-100_2025-10-26_01</a></p>
<p>Large drive wheel (wheel attached to axle being driven by spring)</p>
</td>
</tr>
<!---------------------------------- Third wheel holder -->
<tr>
<td valign="top">
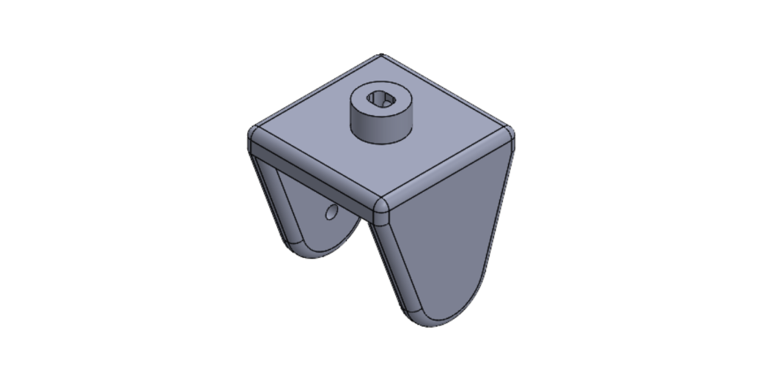
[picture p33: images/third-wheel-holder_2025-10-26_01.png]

</td>
<td valign="top">
<p><a href="third-wheel-holder_2025-10-26_01.SLDPRT">third-wheel-holder_2025-10-26_01</a></p>
<p>Bracket to hold a single wheel and attach to a motor for turning</p>
</td>
</tr>
<!---------------------------------- Third wheel holder - with pointer-->
<tr>
<td valign="top">

</td>
<td valign="top">
<p><a href="third-wheel-holder_2025-11-24_01.SLDPRT">third-wheel-holder_2025-11-24_01</a></p>
<p>Bracket to hold a single wheel and attach to a motor for turning with a guider to see exactly where the wheel is aligned</p>
</td>
</tr>
<!---------------------------------- Small spring tower -->
<tr>
<td valign="top">

</td>
<td valign="top">
<p><a href="spring-tower-100_2025-11-12_02.SLDPRT">spring-tower-100_2025-11-12_02</a></p>
<p>Tower to hold small spring wheel (for getting ~360 degrees from spring)</p>
</td>
</tr>
<!---------------------------------- Small spring tower - reversed -->
<tr>
<td valign="top">

</td>
<td valign="top">
<p><a href="spring-tower-100-reverse_2025-11-23_01.SLDPRT">spring-tower-100-reverse_2025-11-23_01</a></p>
<p>Tower to hold small spring wheel (for getting ~360 degrees from spring) - but reversed to position on the chassis backwards</p>
</td>
</tr>
<!---------------------------------- Large spring tower -->
<tr>
<td valign="top">

</td>
<td valign="top">
<p><a href="spring-tower-200_2025-11-14_01.SLDPRT">spring-tower-200_2025-11-14_01</a></p>
<p>Tower to hold large spring wheel (for getting ~360 degrees from spring)</p>
</td>
</tr>
<!---------------------------------- Spring holder top -->
<tr>
<td valign="top">

</td>
<td valign="top">
<p><a href="spring-holder-top_2025-11-11_01.SLDPRT">spring-holder-top_2025-11-11_01</a></p>
<p>Holds the spring to the spring tower (for getting ~360 degrees from spring)</p>
</td>
</tr>
<!---------------------------------- Spring holder top - reversed -->
<tr>
<td valign="top">

</td>
<td valign="top">
<p><a href="spring-holder-top-reverse_2025-11-23_01.SLDPRT">spring-holder-top-reverse_2025-11-23_01</a></p>
<p>Holds the spring to the reversed spring tower (for getting ~360 degrees from spring)</p>
</td>
</tr>
<!---------------------------------- Small spring wheel -->
<tr>
<td valign="top">

</td>
<td valign="top">
<p><a href="spring-wheel-100_2025-11-12_02.SLDPRT">spring-wheel-100_2025-11-12_02</a></p>
<p>Small spring wheel (for getting ~360 degrees from spring)</p>
</td>
</tr>
<!---------------------------------- Large spring wheel -->
<tr>
<td valign="top">

</td>
<td valign="top">
<p><a href="spring-wheel-200_2025-11-14_01.SLDPRT">spring-wheel-200_2025-11-14_01</a></p>
<p>Large spring wheel (for getting ~360 degrees from spring)</p>
</td>
</tr>
<!---------------------------------- Chassis -->
<tr>
<td valign="top">

</td>
<td valign="top">
<p><a href="Chassis.v1-long_2025-11-24_01.SLDPRT">Chassis.v1-long_2025-11-24_01</a></p>
<p>Chassis of the car</p>
</td>
</tr>
</table>

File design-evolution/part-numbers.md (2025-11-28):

# Parts

<ul>
<li><b>Drive wheels</b>
<ul>
<li><a href="#drive-wheel-xs">Drive wheel (XS)</a></li>
<li><a href="#drive-wheel-s">Drive wheel (S)</a></li>
<li><a href="#drive-wheel-m">Drive wheel (M)</a></li>
<li><a href="#drive-wheel-l">Drive wheel (L)</a></li>
</ul>
</li>
<li><a href="">Axle</a></li>
<li><a href="">Chassis</a></li>
<li><a href="">Spring tower</a></li>
<li><a href="">Turning wheel</a></li>
<li><a href="">...</a></li>
<li><a href="">...</a></li>
<li><a href="">...</a></li>
</ul>

### Drive wheel (XS)
<table>
<tr>
<td valign="top"><b>Part description</b></td><td valign="top">
<p>Smallest drive wheel</p>
<ul>
<li>Radius: 25mm</li>
<li>Cut-outs reduce weight</li>
<li>Groove around outer edge holds elastic band in place for traction</li>
<li>Part file: <a href="../SolidWorks-files/drive-wheel-050_2025-11-12_01.SLDPRT">drive-wheel-050_2025-11-12_01.SLDPRT</a></li>
</ul>
</td>
</tr>
<tr>
<td valign="top"><b>Designer</b></td>
<td valign="top">Sarah Packowski</td>
</tr>
<tr>
<td valign="top"><b>Approver</b></td>
<td valign="top">&nbsp;</td>
</tr>
<tr>
<td valign="top"><b>Part number issued</b></td>
<td valign="top">ALGO_#####</td>
</tr>
<tr>
<td valign="top"><b>Revision</b></td>
<td valign="top">1.0</td>
</tr>
</table>

<p>&nbsp;</p>

### Drive wheel (S)
<table>
<tr>
<td valign="top"><b>Part description</b></td><td valign="top">
<p>Second-smallest drive wheel</p>
<ul>
<li>Radius: 37.5mm</li>
<li>Cut-outs reduce weight</li>
<li>Groove around outer edge holds elastic band in place for traction</li>
<li>Part file: <a href="../SolidWorks-files/drive-wheel-050_2025-11-12_01.SLDPRT">drive-wheel-050_2025-11-12_01.SLDPRT</a></li>
</ul>
</td>
</tr>
<tr>
<td valign="top"><b>Designer</b></td>
<td valign="top">Sarah Packowski</td>
</tr>
<tr>
<td valign="top"><b>Approver</b></td>
<td valign="top">&nbsp;</td>
</tr>
<tr>
<td valign="top"><b>Part number issued</b></td>
<td valign="top">ALGO_#####</td>
</tr>
<tr>
<td valign="top"><b>Revision</b></td>
<td valign="top">1.0</td>
</tr>
</table>

<p>&nbsp;</p>

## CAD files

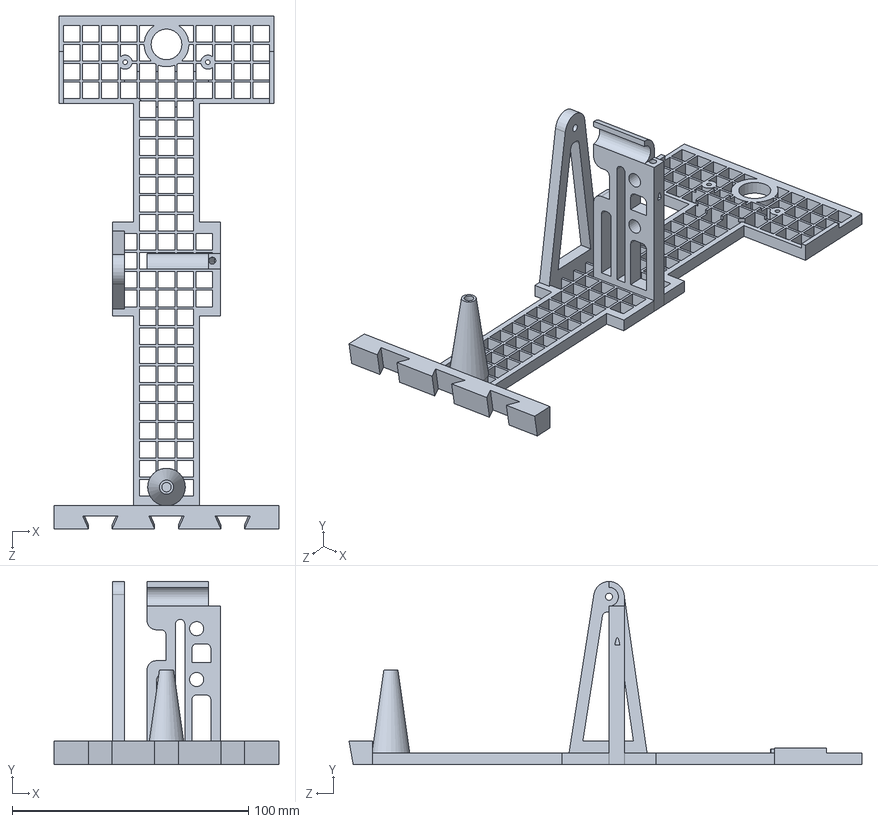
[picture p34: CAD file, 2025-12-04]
SolidWorks-files/chassis_light_2025-12-03.SLDPRT
95.0 x 77.5 x 217.0 mm

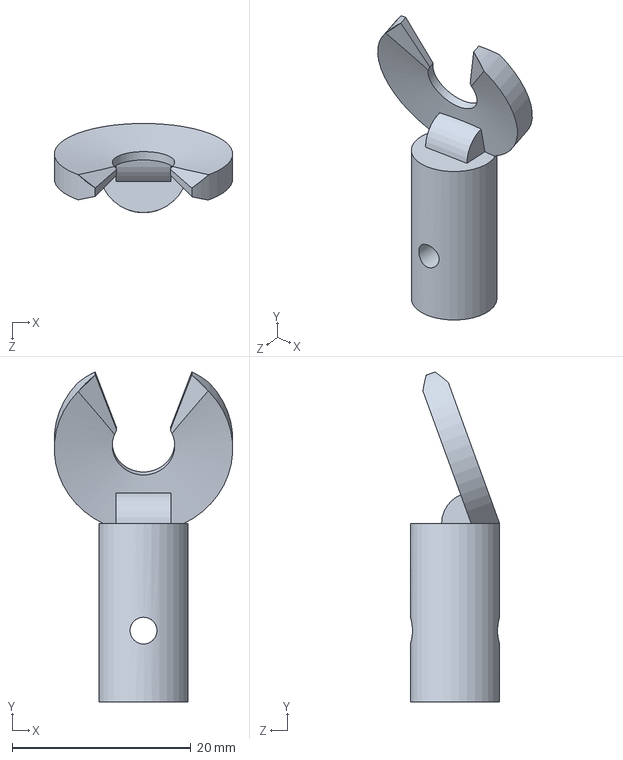
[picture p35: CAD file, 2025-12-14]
SolidWorks-files/final-files/float-holder-final.SLDPRT
20.0 x 37.0 x 10.0 mm

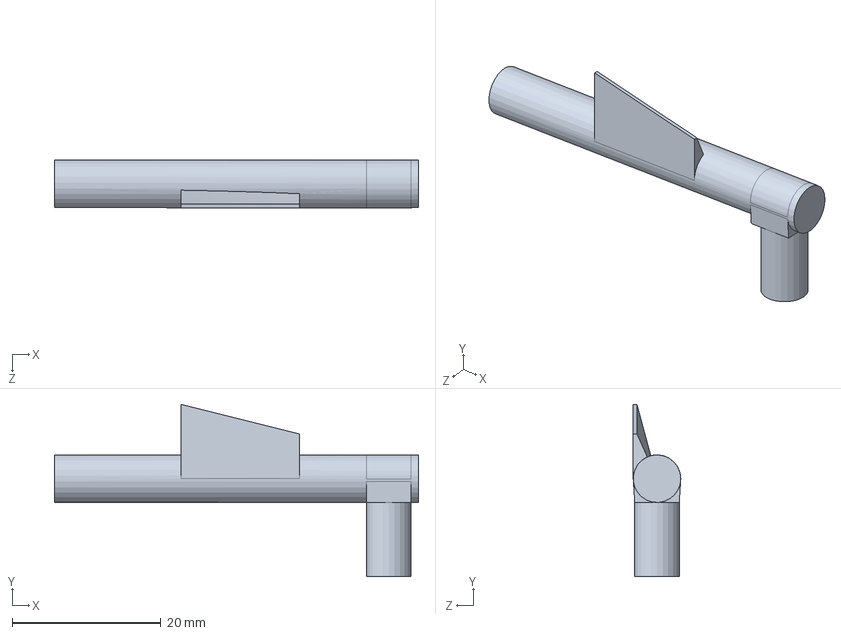
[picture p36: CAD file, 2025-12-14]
SolidWorks-files/final-files/whisker-swivel-final.SLDPRT
49.0 x 23.2 x 6.40 mm

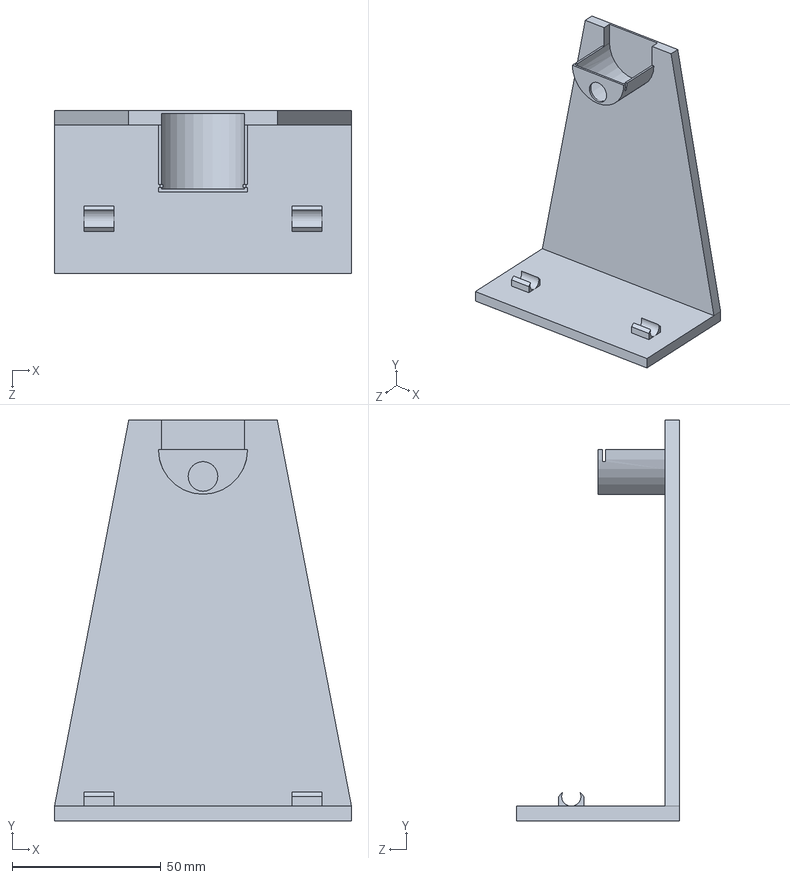
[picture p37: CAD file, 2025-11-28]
SolidWorks-files/Base-New_2025-11-26_02.SLDPRT
100.0 x 135.0 x 55.0 mm

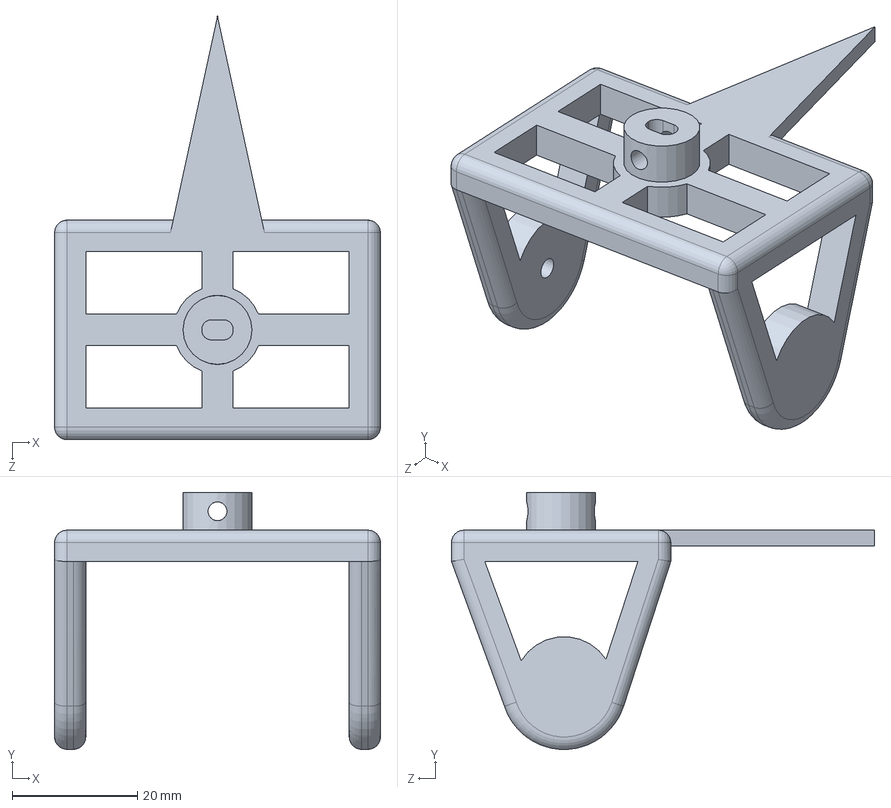
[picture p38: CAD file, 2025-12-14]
SolidWorks-files/final-files/third-wheel-holder-final.SLDPRT
52.0 x 41.0 x 67.5 mm

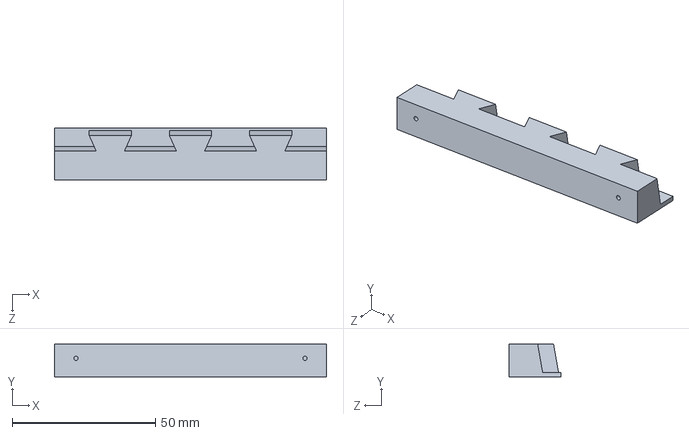
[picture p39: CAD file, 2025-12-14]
SolidWorks-files/final-files/back-bumper-final.SLDPRT
95.0 x 11.5 x 18.0 mm

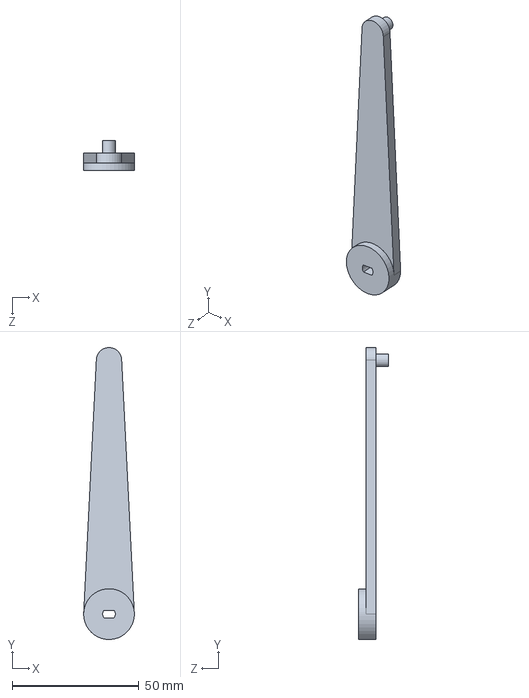
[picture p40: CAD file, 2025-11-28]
SolidWorks-files/Gear-Hat-New.SLDPRT
20.0 x 115.0 x 12.0 mm

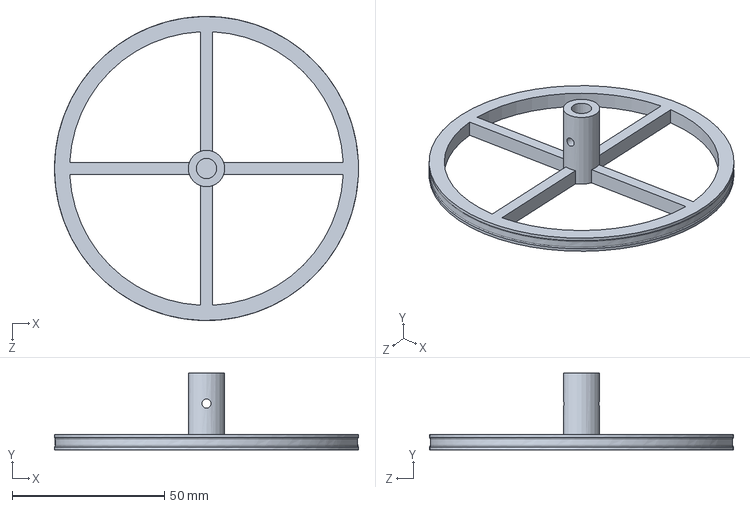
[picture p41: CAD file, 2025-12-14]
SolidWorks-files/final-files/drive-wheel-lg-final.SLDPRT
100.0 x 25.2 x 100.0 mm

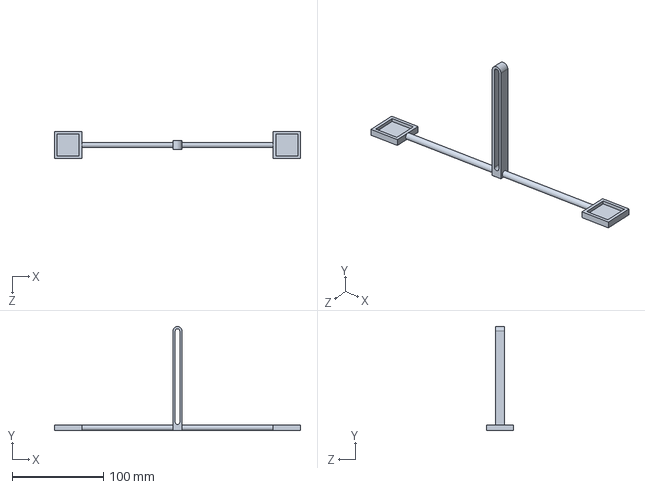
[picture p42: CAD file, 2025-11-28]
SolidWorks-files/Yoke-New_2025-11-26_01.SLDPRT
270.0 x 114.2 x 30.0 mm

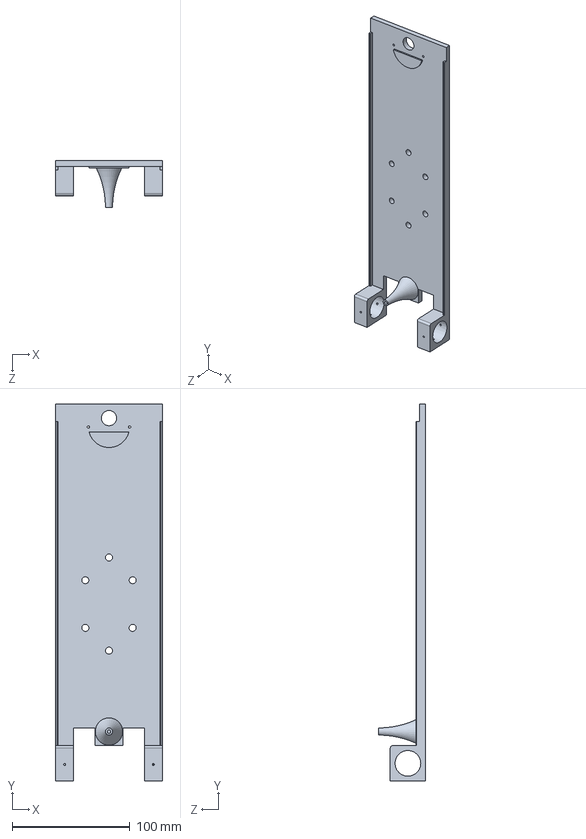
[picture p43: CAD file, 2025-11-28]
SolidWorks-files/Chassis.v1-long_2025-11-27_01.SLDPRT
90.5 x 320.0 x 40.0 mm

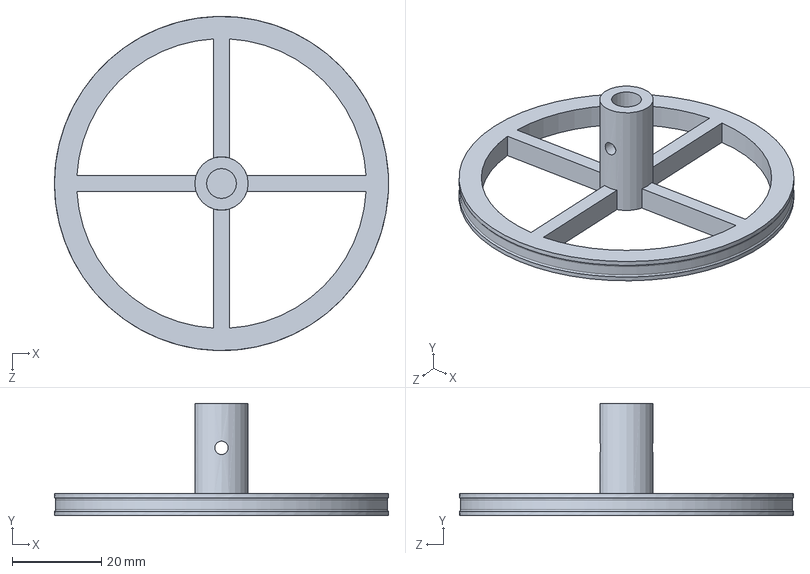
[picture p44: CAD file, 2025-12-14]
SolidWorks-files/final-files/drive-wheel-md-final.SLDPRT
75.0 x 25.2 x 75.0 mm

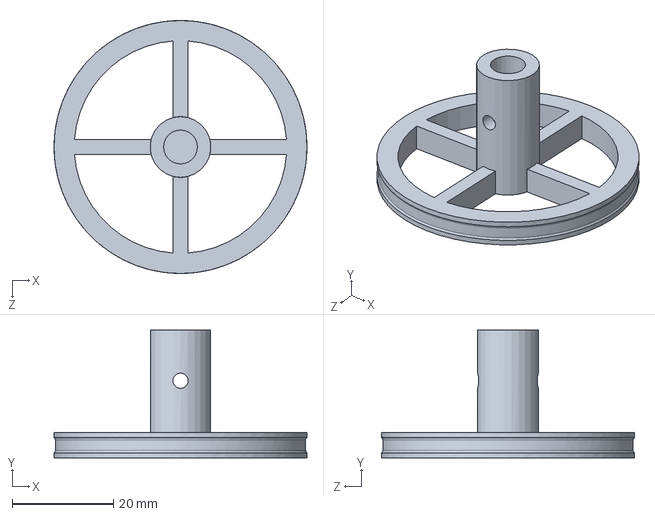
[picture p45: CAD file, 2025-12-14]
SolidWorks-files/final-files/drive-wheel-sm-final.SLDPRT
50.0 x 25.2 x 50.0 mm

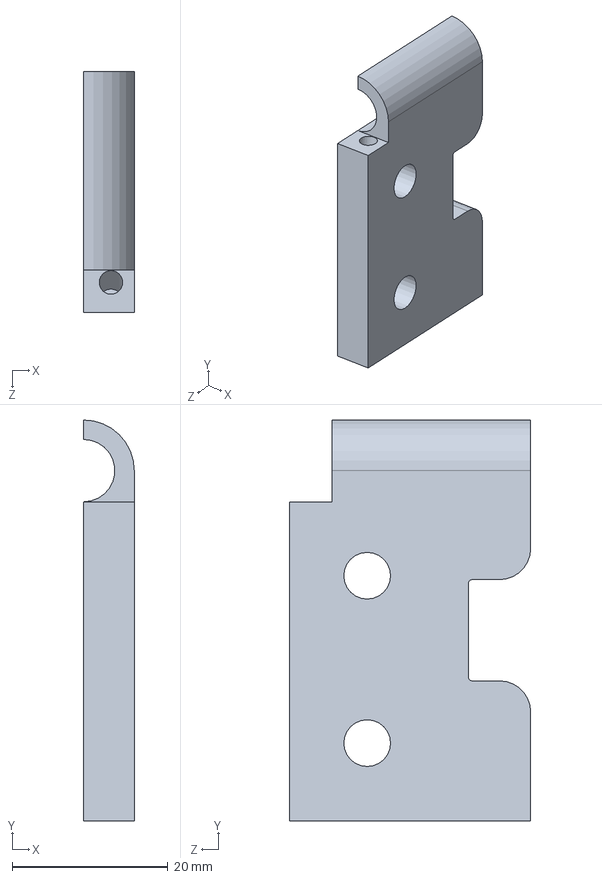
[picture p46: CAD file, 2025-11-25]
SolidWorks-files/spring-holder-top-reverse_2025-11-23_01.SLDPRT
6.50 x 51.5 x 31.0 mm

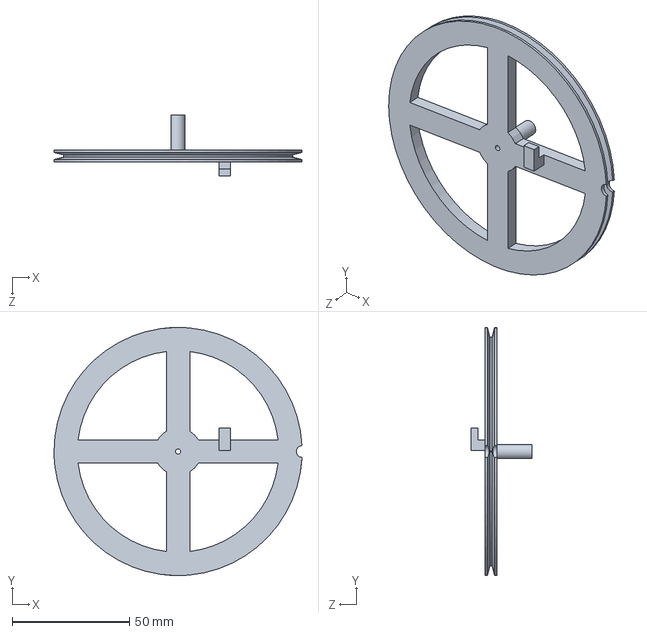
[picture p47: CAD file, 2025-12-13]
SolidWorks-files/final-files/spring-wheel.SLDPRT
105.9 x 106.0 x 26.0 mm

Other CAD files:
SolidWorks-files/car-assembly_2025-11-28.SLDASM
SolidWorks-files/spring-tower-100-reverse_2025-11-23_01.SLDPRT
SolidWorks-files/final-files/spring-holder-final.SLDPRT
SolidWorks-files/third-wheel-holder_2025-11-24_01.SLDPRT
SolidWorks-files/drive-wheel-050_2025-11-12_01.SLDPRT
SolidWorks-files/drive-wheel-075_2025-10-26_01.SLDPRT
SolidWorks-files/drive-wheel-100_2025-10-26_01.SLDPRT
SolidWorks-files/final-files/back-bumper-final.SLDDRW
SolidWorks-files/final-files/chassis_mousetrap_final.SLDDRW
SolidWorks-files/final-files/chassis_mousetrap_final.SLDPRT
SolidWorks-files/final-files/chassis_spring-tower_final.SLDDRW
SolidWorks-files/final-files/chassis_spring-tower_final.SLDPRT
SolidWorks-files/final-files/drive-wheel-lg-final.SLDDRW
SolidWorks-files/final-files/drive-wheel-md-final.SLDDRW
SolidWorks-files/final-files/drive-wheel-sm-final.SLDDRW
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

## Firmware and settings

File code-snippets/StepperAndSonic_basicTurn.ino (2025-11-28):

#define STEPPER_PIN_1 8
#define STEPPER_PIN_2 9
#define STEPPER_PIN_3 10
#define STEPPER_PIN_4 11

#define STEPS_PER_REVOLUTION 2048

#define CLOCKWISE 0
#define COUNTER_CLOCKWISE 1

#define TRIG_PIN 3
#define ECHO_PIN 2

int  g_step_number = 0;

bool g_b_test_done = false;

long duration, cm;

void setup() 
{
   Serial.begin( 9600 );

   pinMode( STEPPER_PIN_1, OUTPUT );
   pinMode( STEPPER_PIN_2, OUTPUT );
   pinMode( STEPPER_PIN_3, OUTPUT );
   pinMode( STEPPER_PIN_4, OUTPUT );
   pinMode( TRIG_PIN, OUTPUT);
   pinMode(ECHO_PIN, INPUT);
}


void loop() 
{
   digitalWrite(TRIG_PIN, LOW);
  delayMicroseconds(2);
  digitalWrite(TRIG_PIN, HIGH);
  delayMicroseconds(10);
  digitalWrite(TRIG_PIN, LOW);

  // The same pin is used to read the signal from the PING))): a HIGH pulse
  // whose duration is the time (in microseconds) from the sending of the ping
  // to the reception of its echo off of an object.
  duration = pulseIn(ECHO_PIN, HIGH);

  // convert the time into a distance
  cm = microsecondsToCentimeters(duration);

  Serial.print(cm);
  Serial.print("cm");
  Serial.println();

  delay(100);
   if( cm <= 60 )
   {
      delay( 10 );
      Serial.println( "Processing object dodge sweep..." );
      turn(COUNTER_CLOCKWISE, 30);
      delay(100);
      turn(CLOCKWISE, 30);
      g_b_test_done = true;
      Serial.println( "Done" );
   }
}


void turn( int direction, float degrees )
{
   float num_steps = ( degrees * STEPS_PER_REVOLUTION ) / 360.0;

   for( int i = 0; i < num_steps; i++ )
   {
      step( direction );
   }
}


void step( int direction )
{
   if( CLOCKWISE == direction )
   {
      firePin( g_step_number + 1 );
   }
   else
   {
      firePin( 4 - g_step_number );
   }

   g_step_number = ( g_step_number + 1 ) % 4;
   
}


void firePin( int pin_num )
{
   digitalWrite( STEPPER_PIN_1, ( 1 == pin_num ) ? HIGH : LOW );
   digitalWrite( STEPPER_PIN_2, ( 2 == pin_num ) ? HIGH : LOW );
   digitalWrite( STEPPER_PIN_3, ( 3 == pin_num ) ? HIGH : LOW );
   digitalWrite( STEPPER_PIN_4, ( 4 == pin_num ) ? HIGH : LOW );
   delay(2);
}

long microsecondsToCentimeters(long microseconds) {
  // The speed of sound is 340 m/s or 29 microseconds per centimeter.
  // The ping travels out and back, so to find the distance of the object we
  // take half of the distance travelled.
  return microseconds / 29 / 2;
}

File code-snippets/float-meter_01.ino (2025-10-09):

// Needed to turn on the light to signal
// the whisker has sensed the block
#include <WiFiNINA.h>
#include <utility/wifi_drv.h>
const int RED = 25;
const int OFF = 0;
const int MEDBRIGHT = 5;

// Needed to track the data coming
// from the float meter
const byte FLOAT_PIN = 8;
int float_state = HIGH;
unsigned long prev_time = millis();

// Track whether the block has been sensed
bool b_sensed = false;

void setup() 
{
   // Log what's happening
   Serial.begin( 9600 );

   // Set up the light
   WiFiDrv::pinMode( RED, OUTPUT );
   WiFiDrv::analogWrite( RED, OFF );

   // Set up the float meter sensor
   pinMode( FLOAT_PIN, INPUT );
}

void loop() 
{
   if( !b_sensed && ( millis() - prev_time ) > 500 ) // See what's up every half second
   {
      float_state = digitalRead( FLOAT_PIN );
      Serial.println( float_state );

      prev_time = millis();

      if( LOW == float_state )
      {
         b_sensed = true;
         WiFiDrv::analogWrite( RED, MEDBRIGHT );
         Serial.println( "Whisker sensed block" );
      }
   }
}

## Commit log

2025-10-09 Add flow meter sample
2025-10-09 Add float meter sample
2025-10-20 Add stepper motor sample
2025-10-21 Added details about sensors and motor
2025-11-25 Add stepper-motor_02.ino (turn by degrees)
2025-11-25 Document stepper-motor_02.ino in README
    Added details about stepper-motor_02.ino functionality.
2025-11-25 Add reversed spring holder top
2025-11-27 Add images of drivetrain evolution
2025-11-27 Add steering evolution
    Added a new section on Chassis and detailed iterations for steering mechanisms.
2025-11-27 Different link for stepper motor datasheet
2025-11-27 Add chassis evolution to date
2025-11-27 Add wheel evolution
2025-11-28 Add basic stepper motor control with ultrasonic sensor
